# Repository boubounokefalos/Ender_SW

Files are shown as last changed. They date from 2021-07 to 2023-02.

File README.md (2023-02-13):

# Ender 3 Pro/V2 to Switchwire Conversion Release.2

This is a full conversion of the popular Ender 3 Pro/V2 to a Voron Switchwire. The motivation came from [Triano](https://github.com/walttriano) and [his awesome original conversion](https://github.com/walttriano/VoronUsers/tree/master/printer_mods/Triano/Ender_3Pro_Switchwire) that served as a starting point, however everything was re-designed from scratch (in order to follow the Voron guidelines and aesthetics more accurately). Another factor that led to this re-design, was the need to be able to enclose this printer in a, visually, pleasant and, structurally, functional way. The ingenious design of 5x MGN12H Linear Rails - 300mm (dual Y axis rail) from Triano was preserved and the printing volume is ~220x220x220.

# Release 2 Update Changelog:

- CAD files cleaned up.
- Small corrections to parts.
- Added printable deck files (still it's recommended to laser cut them though)
- Added different .dxfs for rear black panels (in case anyone wants to cut the panels from a material that is not same on both surfaces)
- Added the option to use the stock Ender 3 LCD screen.

# Rev.2 Update Changelog:

- Every change happened in order to improve the build process and the design overall.
- All screw sizes and types are properly documented in the CAD (soon there will be a conversion BOM also). Also no more “exotic” sizes, everything is according to what VORON is using officially.
- Current conversion’s enclosure is 100% compatible with the new update (except of the deck panels ofc).
- XZ Blocks improved fit for the X v-slots and are also modified to use 30mm BHCS (like the original SW).
- Y Axis, new front idler (in order to achieve a mounting point for the front grill), improved clearance for the rear Y motor mount. All use BHCS screws now.
- Split bed carriage with size and clearance corrections. Made uppon the design recommendation of Steve. Also Y belt clips have a bit more clearance on the upper side, in order to leave some space for spare belt 🙂
- XZ motors have thinner XZ tensioners to avoid the lower “split” (kudos to Steve for that ALSO).
- We are now using the original SW Spool Holder (for easier installation, due to clearance)
- Front Grills have now the LCD mount of the original SW. They also mount to the extended sides just by M3 screws.
- Rear Grills mount by M5x16 BHCS screws now. Also the inlet has moved to the side (in order to have a straight and easier connection with the PSU), this was also a recommendation by Steve and he was more than kind to share his original .F3D file. Both stock Ender and C14 inlets are compatible.
- Removed material from the grills, in order to save some plastic and cut down print time.
- PSU is now mounted parallel to the side extrusions and RS25 can be mounted in the front of the printer.
- Redesigned mounts for the Board and RPi (no more shelf and moooahr clearance!)

And last but not least…
-The side extensions. Front and rear side extensions are designed to extend the frame for aesthetical and a few practical reasons (clearance and NO MORE NOTCH). They are sturdy enough but keep in mind that you will not move around the printer by lifting it from there.

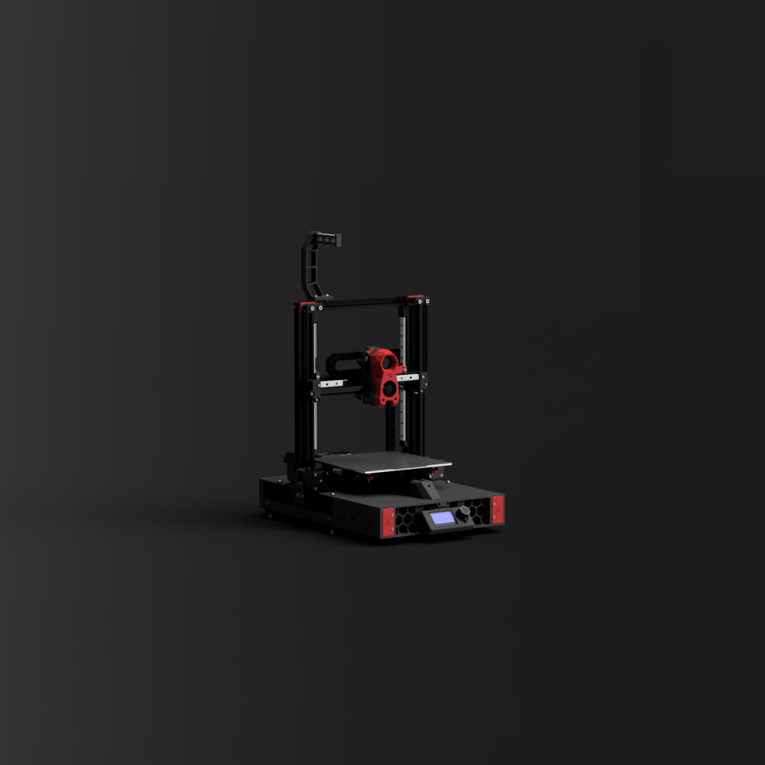
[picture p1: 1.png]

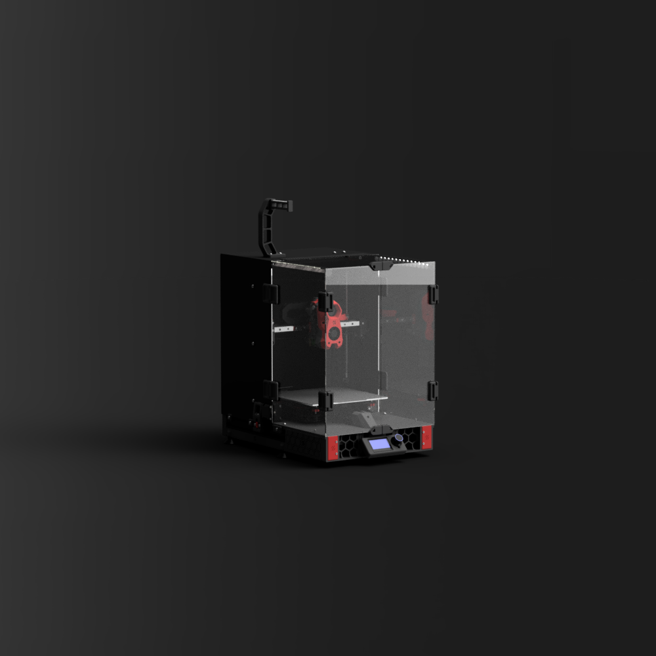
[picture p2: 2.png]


## Info

Various parts _can*_ be recycled from the Ender 3 Pro/V2, most important ones are:
- The frame (though a 310mm extrusion is needed for the X. You can chop the original one to length).
- The MeanWell PSU.
- The heatbed assemble.
- The original board.
- XYZ motors (as long as you can pull off the pulleys. An aftermarket 20mm motor is needed for the printhead extruder though).
- All the cables that don't go through the cable-chains (for there, silicone or PTFE cable is adviced).
- 4010 fan for the tool cooling.

*cheaping out in parts can lead into several problems, such as poor printing quality or, even worse, safety hazard. Keep that in mind and use parts from the official Switchwire BOM.

## Files

- Most of the printed part files needed for this conversion, are included in this git (you will only need to get the Stealthburner print files from the [official Switchwire git](https://github.com/VoronDesign/Voron-Stealthburner) ).
- CAD files (.f3d and .STEP) are provided, in order to help the building process, but they also serve as a BOM (in case you need to find proper screw lengths etc).
- DXF files in order to cut your enclosure panels.
- BOM (Sometime...)

## Credits

- Ofc to Triano, as his design served as base.
- To Steve (THE Steve!) for pointing out weak parts, that had to be redesigned, his tips and files and being a helpful person in general.
- To sdukan#9213 for his valuable help into troubleshooting the Ender 3 V2 differences, electronics (and in general).
- To all of this awesome community of people and especially the [ender_conversion_chat](https://discord.com/channels/460117602945990666/947303252372906014).
- To Voron design team for all the valuable resources and the solid base.

## Disclaimer

This is a very carefuly designed build.. however mistakes could have been made. By deciding to build this conversion, you are responsible for any possible damage done to the printer or even yourself.

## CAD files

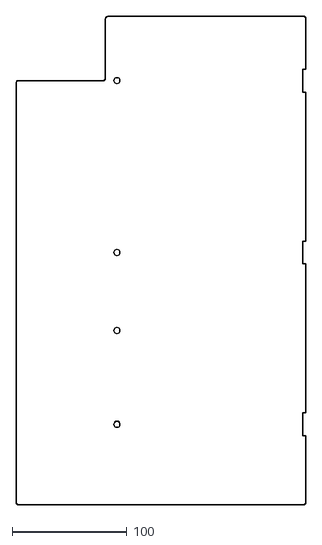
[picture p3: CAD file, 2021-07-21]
DXF/BLACK/M4_compatible/rear_side_panel_x2_M4_compatible.dxf
253.0 x 426.0

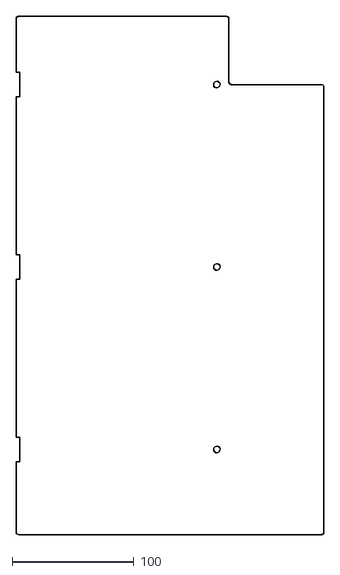
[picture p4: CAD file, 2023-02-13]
DXF/BLACK/rear_side_panel_right.dxf
253.0 x 426.0

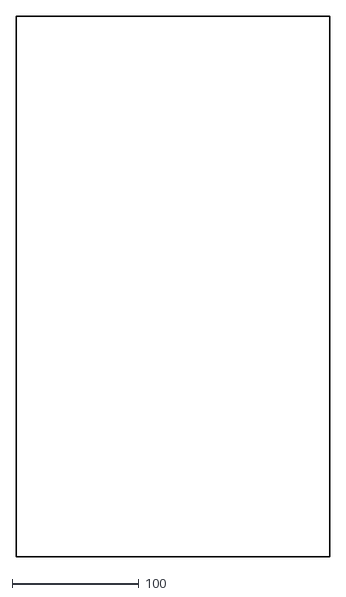
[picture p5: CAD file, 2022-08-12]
DXF/CLEAR/front_side_clear_x2.dxf
247.0 x 426.0

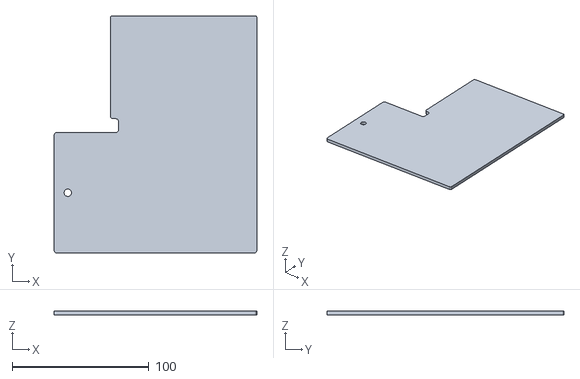
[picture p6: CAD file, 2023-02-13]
STLS/Decks_Printable/deck_left_mid.stl
148.0 x 173.0 x 3.00

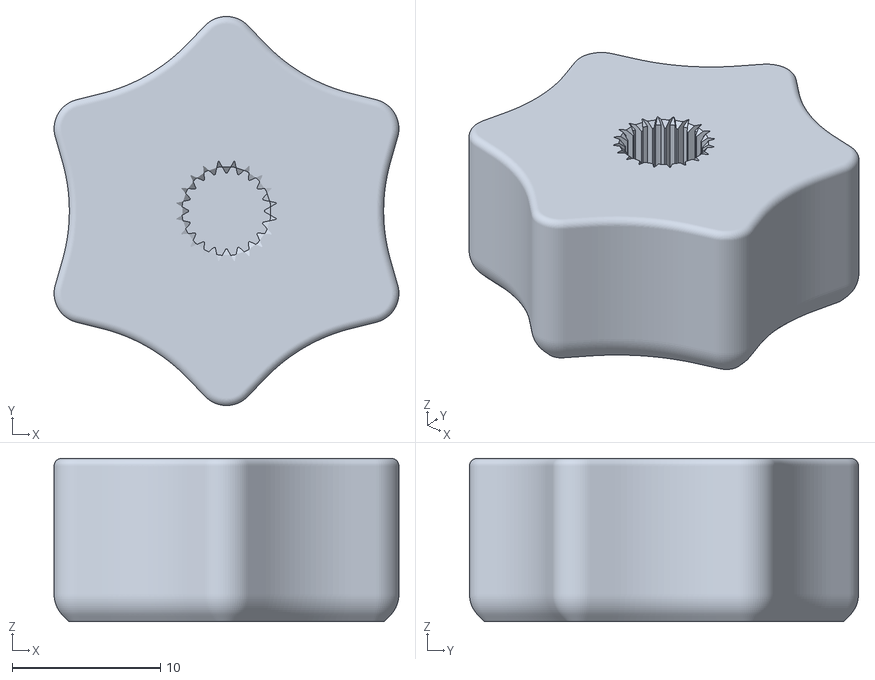
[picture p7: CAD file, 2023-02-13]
STLS/Electronics/Ender_Stock_Screen/[a]_knob.stl
23.3 x 26.2 x 11.0

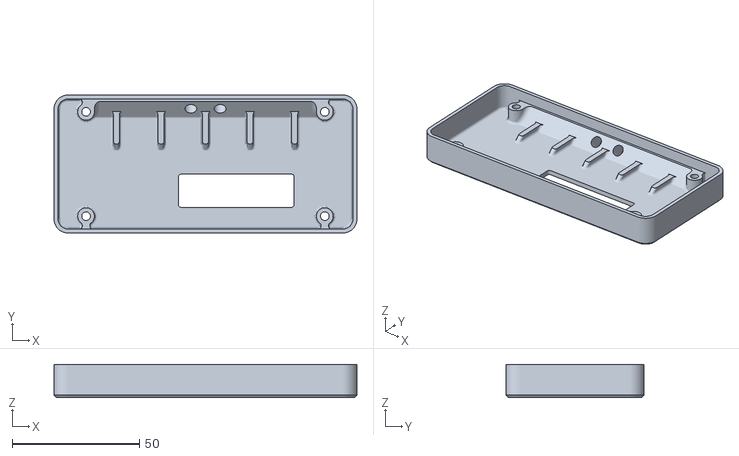
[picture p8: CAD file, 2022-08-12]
STLS/Electronics/Mini12864/lcd_case_rear_mini12864.stl
119.0 x 54.2 x 13.0

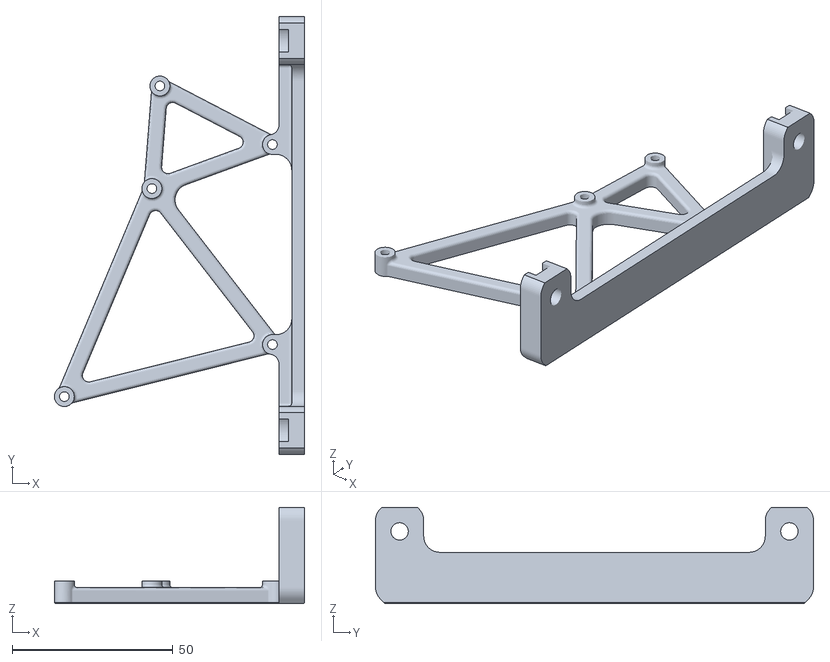
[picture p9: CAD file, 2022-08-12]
STLS/Electronics/skr_mini_e3_mount.stl
77.8 x 136.2 x 30.0

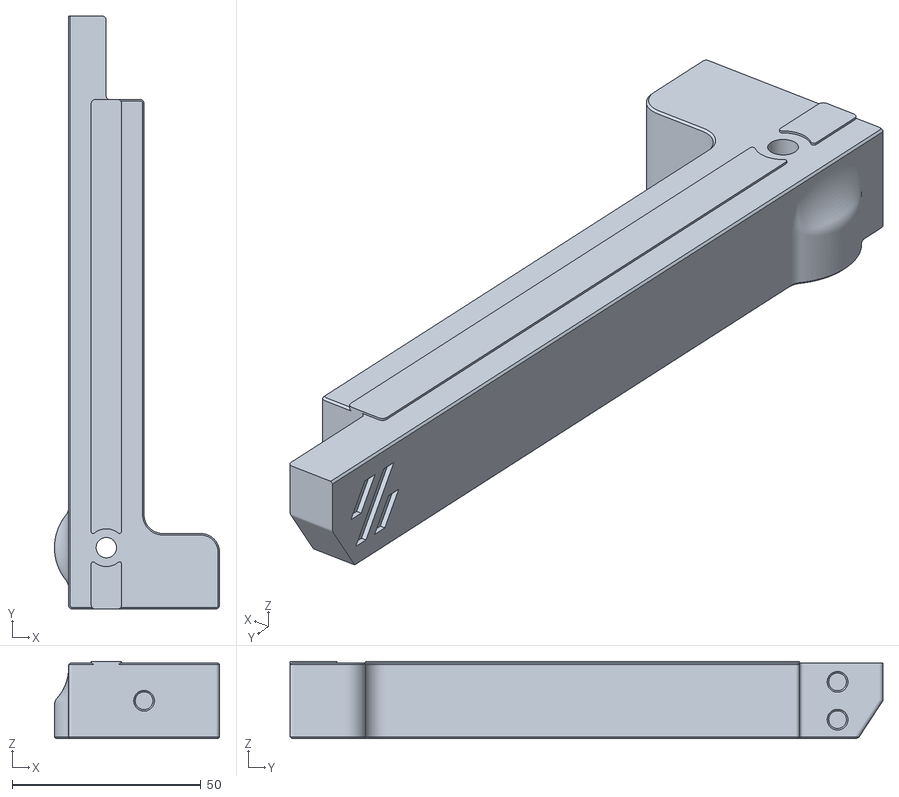
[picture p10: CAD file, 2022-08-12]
STLS/Extentions/rear_extention_right_b.stl
43.8 x 157.1 x 20.4

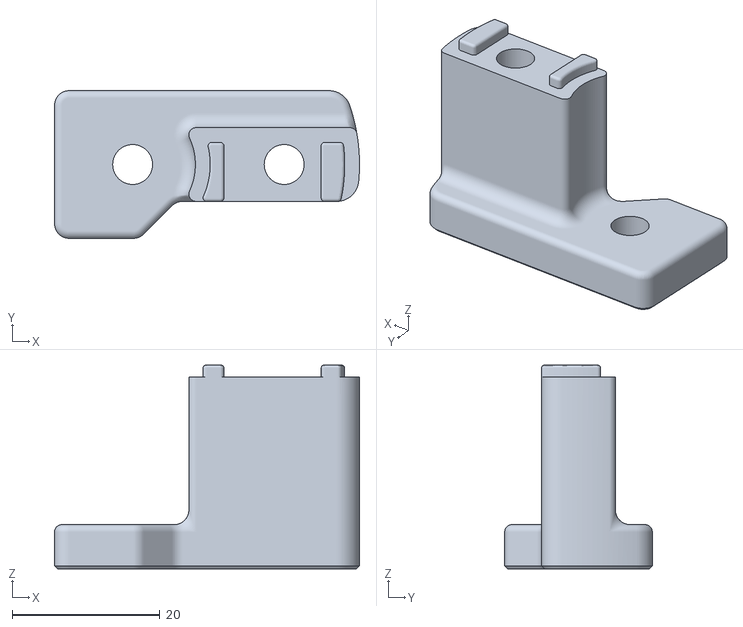
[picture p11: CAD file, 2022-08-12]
STLS/Gantry/XZ Axis/upper_idler_support_a_right.stl
41.3 x 20.0 x 27.6

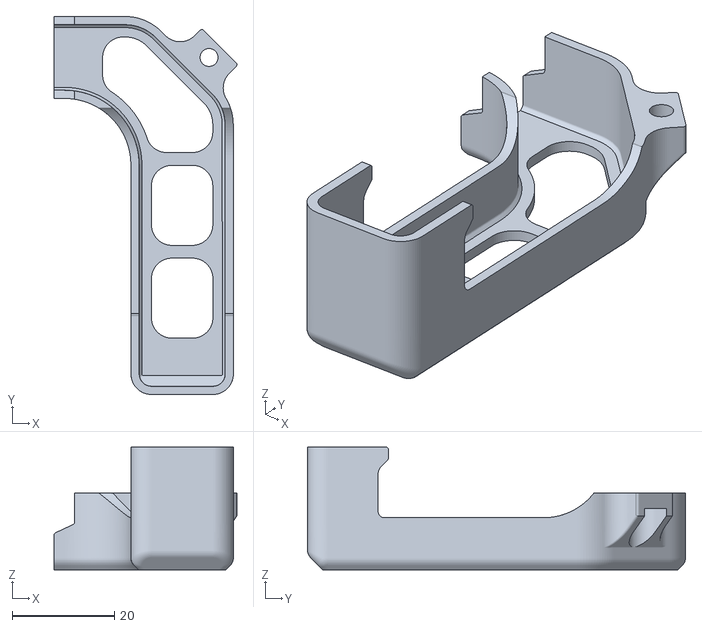
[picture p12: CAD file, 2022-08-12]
STLS/Gantry/XZ Axis/X Axis/[a]_xz_cable_cover.stl
35.7 x 73.8 x 24.0

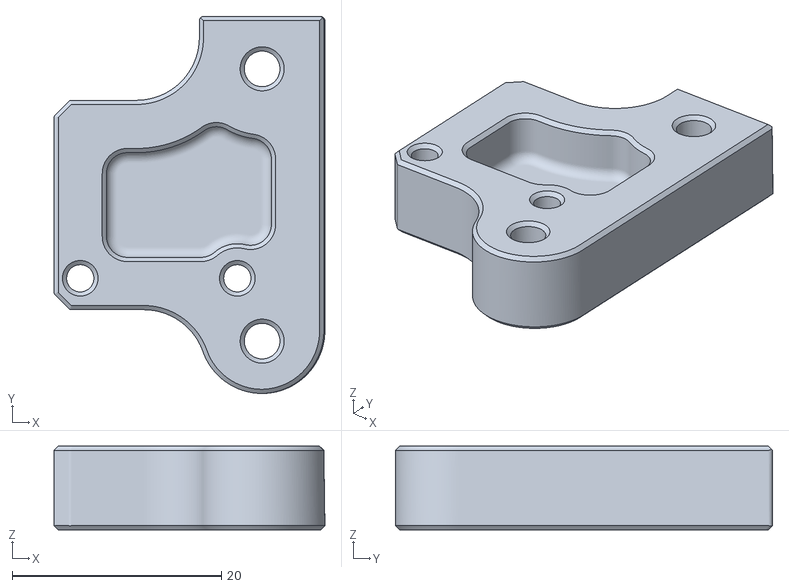
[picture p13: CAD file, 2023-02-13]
STLS/Gantry/Y Axis/[a]_y_axis_ls_mount.stl
25.9 x 36.0 x 8.00

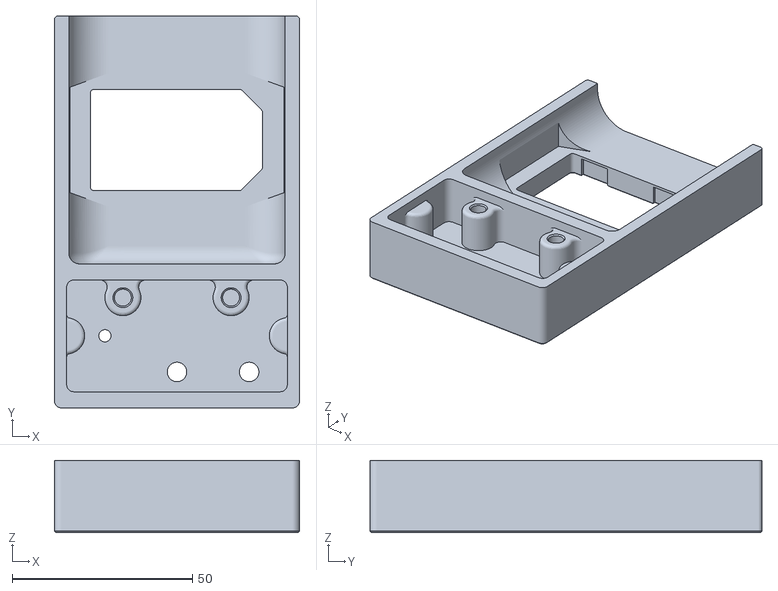
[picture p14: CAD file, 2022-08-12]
STLS/Grills/grill_rear_left_c14_inlet.stl
68.0 x 108.7 x 20.0

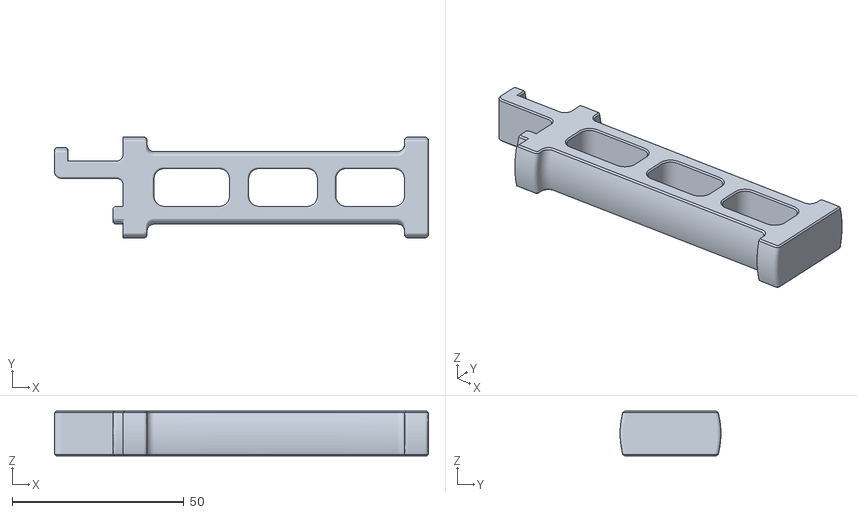
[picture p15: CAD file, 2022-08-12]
STLS/Misc/spool_holder.stl
109.0 x 29.4 x 13.0

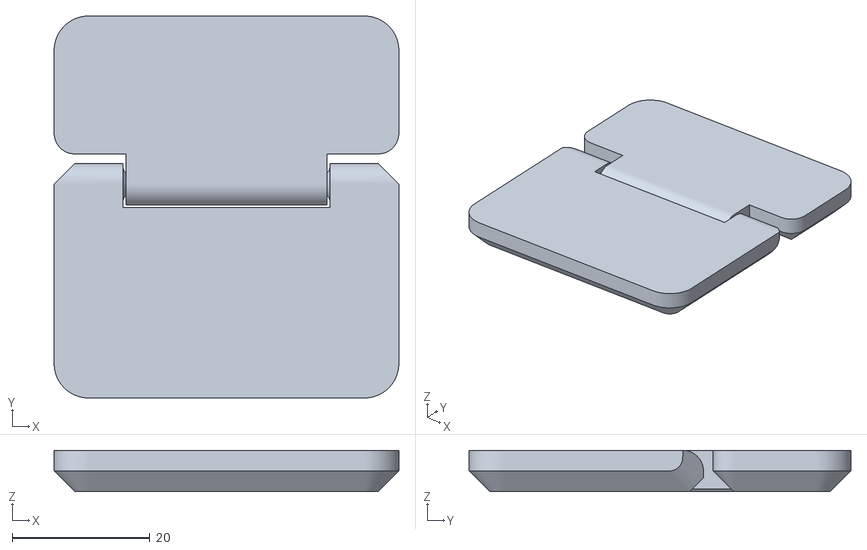
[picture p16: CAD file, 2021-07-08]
STLS/Panel_Mounting/Doors/door_hinge_x4.stl
50.0 x 55.4 x 6.00

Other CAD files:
STLS/Panel_Mounting/front_panel_bracket_left.stl
DXF/BLACK/deck_panel_right.dxf
DXF/CLEAR/front_top_clear.dxf
STLS/Decks_Printable/deck_left_rear.stl
DXF/BLACK/bottom_panel.dxf
DXF/BLACK/deck_panel_left.dxf
DXF/BLACK/rear_panel.dxf
DXF/BLACK/rear_side_panel_left.dxf
DXF/BLACK/top_rear_panel.dxf
DXF/CLEAR/front_clear_door_x2.dxf
STLS/Decks_Printable/deck_left_front.stl
STLS/Decks_Printable/deck_right_front.stl
STLS/Decks_Printable/deck_right_mid.stl
STLS/Decks_Printable/deck_right_rear.stl
STLS/Electronics/Ender_Stock_Screen/Grill.stl
STLS/Electronics/Ender_Stock_Screen/lcd_case_front_ender_lcd.stl
STLS/Electronics/Ender_Stock_Screen/lcd_case_rear_ender_lcd.stl
STLS/Electronics/Mini12864/lcd_case_front_mini12864.stl
STLS/Electronics/PS_4040_Slide_Mount.stl
STLS/Electronics/PS_4040_mount_x2.stl
STLS/Electronics/RPi_bracket.stl
STLS/Electronics/rs_25_mount.stl
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

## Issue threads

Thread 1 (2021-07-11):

Incorrect name for PS_2020_mount_b.stl

mdsamir15790, 2021-07-11:
Please update the PS_2020_mount_b.stl name. As per CAD it should be PS_4040_mount_b.stl

boubounokefalos, 2021-07-11:
@mdsamir15790 good observation! Thanks for that, the correct name is set now :)

Closed 2021-07-11.

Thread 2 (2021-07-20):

Add DXF for deck panels

retsamedoc, 2021-07-20:
It would be nice if you could create a DXF file for the deck panels (preferably in the same two piece configuration as the stock SW) so they could be laser cut?

boubounokefalos, 2021-07-20:
> It would be nice if you could create a DXF file for the deck panels (preferably in the same two piece configuration as the stock SW) so they could be laser cut?

Sure thing mate. Keep in mind though that these panels are cut from 3mm thick acrylic, while the front grills exceed the 4040 extrusions by 4mm (same as the printable deck panels). Will close this once they are added.

retsamedoc, 2021-07-20:
So 4mm material for deck panels would be ideal. I'm currently using coroplast (seems to be about 4mm thick).

boubounokefalos, 2021-07-21:
The DXF directory is updated with the files for the 2 decks, closing the issue now :D

Closed 2021-07-21.

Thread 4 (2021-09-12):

Question upper idler.

WalnutFox, 2021-09-12:
Just curious as to why the upper idler was changed, this would now require 2 m5x40 rather than 1. If this affects the BOM can you please update.

boubounokefalos, 2021-09-12:
The original upper idlers are protruding from the top extrusion. That prevents the printer from being able to be enclosed, without some ugly gimmick solution. Therefore, top idlers had to be re-designed from scratch.
Also keep in mind that the most accurate BOM for this conversion (at least for the screws), is the CAD itself.

Closed 2021-09-12.

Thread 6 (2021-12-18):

BOM

cchance27, 2021-12-18:
Love the look especially with the enclosure was looking into doing the conversion on my new Ender3Pro, but don't see any BOM for what can be reused vs what i'm going to have to order do you have one for the project? No XLSX or anything, just sorta got to look at the cad?

Especially for the enclosure parts

laserbeak, 2022-03-20:
Yes, is the enclosure the same as the Voron BoM?

Deep-Inspiration, 2022-03-20:
The enclosure is completely one-off and shares nothing with the official Switchwire.

laserbeak, 2022-03-21:
Gotcha. Works for me. Thanks.

Closed 2022-01-25.

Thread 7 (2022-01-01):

Missing M5x10 SHCS screw from Wiki

renjie-teo, 2022-01-01:
Hi! I've realised that M5x10 SHCS is a non-Voron BOM spec screw but its missing from the wiki, I had to order some midway building as i couldn't assemble my Y idler and motor, hope you can help add in the wiki for others!

Deep-Inspiration, 2022-01-25:
M5x10 SHCS isn't in the BOM but there are plenty of M5x10 BHCS in the BOM which should substitute just fine.

t0m-r1dd1e, 2022-03-18:
Also ran into this issue during assembly today. Fortunately I started with the Y axis so I can work on other things while I wait for these bolts.

bgct9a, 2022-04-16:
Another fastener issue is that BOM has only 6 M5x40 SHCS while the Cad Uses 8. You can recycle 2 of the m5 x 45's that are removed from the original Ender with some washers. This works as a solution for one of the Z bearing blocks.

bgct9a, 2022-04-16:
Going to Add 4 BHCS M5 x 35mm and 2 BHCS M3 x 14. The M3 x 14 was able to be substituted by an BHCS M3 x 16

boubounokefalos, 2022-08-13:
Closing this, since Rev.2 include all the proper sizes in the CAD model.

Closed 2022-08-13.

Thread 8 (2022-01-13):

Z Probe options and Klicky Probe

harshitgoel96, 2022-01-13:
Hi, I dont have access to genuine Omron Probe. I was look to use a clicky probe like quickdraw or Klicky probe. Do you have any working option for clicky probe? or can it be desinged around this conversion?

cchance27, 2022-01-19:
i haven't tested it but there is ... https://github.com/hymness1/VoronUsers/tree/master/printer_mods/hymness1/Quickdraw_probe_Voron_Switchwire

harshitgoel96, 2022-01-19:
That needs modification due to different extrusion size. And bed height.

I found this one to be very interesting option

https://github.com/salveoo/voronmods/tree/main/Switchwire%20Magprobe

boubounokefalos, 2022-08-13:
Closing, since there are lots of options by several members of the community.

Closed 2022-08-13.

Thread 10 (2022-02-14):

XZ Blocks don't quite fit v-slots, don't sit square, leg underneath extrusion doesn't extend all the way across.

strayr, 2022-02-14:
See image from interference analysis, the parts don't quite sit straight. There's a leg that needed extending as well that helps keep the parts square. I've made some fixes. https://github.com/strayr/Ender3_switchwire_fixes/tree/main/XZ-blocks.

I've done a T-slost version as well as I didn't want to cut up my ender 3.

I hope this is helpful, I'm not sure if I should be posting issue here or to triano's verion 2?

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

lowtolerance, 2022-03-18:
I’m in the middle of building this conversion, and I haven’t gotten around to assembling the XZ blocks. I’ll print these out and compare when I get a chance.

lowtolerance, 2022-03-25:
I forgot to actually print the modified XZ blocks made by strayr, and ended up using the cut edge of the Misumi extrusion like a double-sided plane to shave the parts until the alignment tabs fit snugly into the groove of the extrusion.

boubounokefalos, 2022-03-28:
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

Hello @strayr,

The reason behind this difference is to make the part "clamp" while it gets tightened by the screw on the v-slot groove of the extrusion. It was intended to be like that (this is also done to several other parts of the mod).

strayr, 2022-03-29:
I can't get it to sit straight on the extrusion, although that's probably
the corners not the v-slot, I went through a few iterations before I found
something that worked for me. Maybe you're printing in something that
shrinks less or is more compliant? I'm using eSun ABS+

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

boubounokefalos, 2022-08-13:
Hello mate,

This was carefully considered in the new Rev.2 and was modified accordingly.

Cheers!

Closed 2022-08-13.

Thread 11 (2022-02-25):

can this be made to support the mk52 bed

jaymoore962, 2022-02-25:
since the ender 3 has warping problems with the bed can you add support for the mk52 bed

Deep-Inspiration, 2022-02-25:
> since the ender 3 has warping problems with the bed can you add support for the mk52 bed

The Mk.52 is 17mm wider than the Ender bed and cannot physically fit in the Ender frame.  The only way to fit the Mk.52 is to buy an actual Switchwire frame.

boubounokefalos, 2022-03-08:
>

Correct! The dimensions are nowhere near, plus there is a whole different way the Y is designed.

Closed 2022-03-08.

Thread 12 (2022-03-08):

Ender 3 Compatibility

michaelmyc, 2022-03-08:
Is this compatible with the original Ender 3? I think the big issue will be the 40x40 extrusion on the Y, right?

boubounokefalos, 2022-03-08:
Unfortunately no. Apart from the Y extrusion, there are a few other key differences between 3 and 3pro.

Dilepa, 2022-03-20:
I started off with your mod on a ender 3, but can you please let me know what the other differences are other than Y?

Dilepa, 2022-03-20:
I have already modified the Y idler, Y motor mount and a 2020 spacer to lift the y axis. Anything else?

sparky3387, 2022-03-25:
Just want to leave a comment directing other people looking for this to [https://github.com/VoronDesign/VoronUsers/tree/master/printer_mods/Ultrawaffles/Ender_3_to_SW](https://github.com/VoronDesign/VoronUsers/tree/master/printer_mods/Ultrawaffles/Ender_3_to_SW)

Closed 2022-03-08.

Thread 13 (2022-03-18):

Can’t mount grills or 4040 extenders on Ender 3 v2

lowtolerance, 2022-03-18:
I just went to install the front grill on my Ender 3 v2 and realized that mine does not have tapped holes for the two outer 4040 extrusions, so I can’t mount the front and rear grills as designed.

I was thinking about modifying the front 4040 extenders so that the front grill bolts to them directly, and then the extenders could slot into the V-slot grooves, but I’m concerned that it won’t be strong enough with the weight of the enclosure and display.

Is it possible to buy new extrusions with the holes already drilled in the right places for mounting the Z profiles and the 4040 that goes between these two? Tapping the holes myself is not something I’m equipped for.

Any guidance on how I should proceed would be appreciated.

plasticboat, 2022-03-18:
I encountered the same thing. Honestly I just bought an HSS M5 tap and tap handle from Amazon and took my time. I was easily able to tap the eight holes required on the RH 4040 extrusion.

lowtolerance, 2022-03-18:
Hand tapping them didn’t even occur to me, but I guess it can’t be that hard if the holes are already there. I ordered a kit, thanks for the advise

plasticboat, 2022-03-18:
You're welcome. I do think the readme should warn people about this though in my opinion. I didn't realize it myself until I was pretty committed to this build.

t0m-r1dd1e, 2022-03-18:
Yeah grab a cheap tap set. They work fine for aluminum and you'll be glad you have them in the future.

lowtolerance, 2022-03-19:
I got a cheap tap set for $10 and managed to tap all 16 of these holes in about 30 minutes. Thanks for the advice.

Closed 2022-03-19.

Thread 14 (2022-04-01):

update printer.cfg

tol2cj, 2022-04-01:
Please correct usage of default parameter values in cancel_print and pause
 like this:
#default_parameter_X: 220
#default_parameter_Y: 220
#default_parameter_Z: 10
gcode:
    {% set X = params.X|default(220) %}
    {% set Y = params.X|default(220) %}
    {% set Z = params.X|default(10) %}

boubounokefalos, 2023-02-13:
Due to a wide variety of configurations nowdays,
I will no longer be including configuration files.

Cheers!

Closed 2023-02-13.

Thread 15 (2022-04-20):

Missing foot screws from CAD and BOM

ndanyluk, 2022-04-20:
Hi, thanks so much for your awesome work on this!

I'm opening this issue because when searching through the .f3d file I can't seem to find any screws attaching the feet to the frame.  I assume since the extensions are 20mm tall that we probably want something like M5x25 or 30mm but I couldn't tell.  Do you have a particular screw spec'd for this part?

About to order my screws for the build and want to be sure I grab em all :)

boubounokefalos, 2022-08-13:
Hello mate,

No screw size is stated regarding the feet due to the fact that most people use different feet (regardless the included air compressor rubber ones).

Closed 2022-08-13.

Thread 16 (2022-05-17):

cover_4040_extrusion_cut_enderV2 is not wide enough ..

piotrb, 2022-05-17:
On my V2 the cutout is ~40mm (not 35 as this STL expects) ..
it also looks like its been cut out "more"? .. the intended clip in the current design won't catch on anything there ..

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

boubounokefalos, 2022-05-17:
> On my V2 the cutout is ~40mm (not 35 as this STL expects) .. it also looks like its been cut out "more"? .. the intended clip in the current design won't catch on anything there ..
>
> 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

Unfortunately there are quite a few iterations of Ender V2 with differences I cannot follow up (since I don't own this machine). This specific cable cover was designed with the help of a friend that had this exact dimensions (on his Ender 3 v2)

Closed 2022-05-17.

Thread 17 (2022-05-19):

4040_rail_tool stl missing

bob92553, 2022-05-19:
[4040 rail tool.zip](https://github.com/boubounokefalos/Ender_SW/files/8734505/4040.rail.tool.zip)

matthewdolman, 2022-12-04:
Thank you!

Closed 2023-02-13.

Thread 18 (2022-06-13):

mounting the enclosure

flow1990, 2022-06-13:
I can't find anything about mounting the printed parts to the enclosure. Is the tape used here?

boubounokefalos, 2022-06-25:
It's the exact same way as the original SW (VHB tape)

Closed 2022-06-25.

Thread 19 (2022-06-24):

Ender 3 V2 - X extrusion is wrong size ..

piotrb, 2022-06-24:
Seems like the model calls for a 310mm X gantry extrusion .. seems like my Ender 3 v2 uses a 350mm one there.

I'm reluctant to cut it (since once its done there is no going back there ;) .. really gotta get all my parts assembled and ready before I do this next step .. was hoping I was going to be able to be a bit gradual, but this one part seems to require a permanent modification.
It seems like the whole design depends on that extrusion being a but shorter than its wide so it seems like its kind of key to note that for folks.

The instructions should include something about potentially needing to do this :)

Perhaps in the wiki around the frame section.

boubounokefalos, 2022-06-25:
This is stated at the first lines of the "Info" section (310mm info for the X). This is not a modification that can be done gradually.

Closed 2022-06-25.

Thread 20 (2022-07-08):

BOM Difference: MGN12 Rails

ardichoke, 2022-07-08:
The BOM page in the wiki should note that a 5th MGN12 rail is needed for this conversion, since the official BOM for the Switchwire only requires 4.

I'd submit a pull request for it.... but you know, can't do PRs on the wiki repo. Thanks GitHub.

boubounokefalos, 2022-08-13:
Hello mate,

5xMGN12 is stated on the README :)

ardichoke, 2022-08-14:
Sure, but if you're going to have a BOM in the Wiki that lists the additional items you need, it should be complete, and it currently isn't. I ordered parts based on the stock BOM + the items listed in the BOM in the wiki and then had to order another rail once I started actually building because of that.

Closed 2022-08-13.

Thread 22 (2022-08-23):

BOM?

lordmach, 2022-08-23:
Where is the BOM? I cannot find it anywhere in the files. Thank you.

boubounokefalos, 2022-08-23:
BOM will be available soon (only for Rev.2) as stated.

lordmach, 2022-08-23:
I watched this build on Steve's channel and got an Ender to start it. Do you mind sending my the BOM? Thanks for all your effortsBTW.

boubounokefalos, 2022-08-23:
The BOM will be released once it's fully ready for everyone. Till then, CAD serves as BOM.

Cheers :)

lordmach, 2022-08-23:
OK. Ill get it from Steve.

Thanks anyway...

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

--
Regards,

Joe Costa

aforww, 2023-01-21:
It's been five months, any updates?

boubounokefalos, 2023-01-21:
> It's been five months, any updates?

Robotrogue has uploaded a basic BOM that can help you >>> https://github.com/RobotRogue/Enderwire_Docs

Closed 2022-08-23.

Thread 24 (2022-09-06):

Rev. 2

DoCJEaa, 2022-09-06:
Hello,
Is there a way to reach you via Discord or something like that? I have a few ideas for Rev. 2.

petternilsen, 2022-09-06:
Yes, the voron discord have a thread under switchwire for ender conversions.

LukasM82, 2022-09-08:
Go here, it's called #ender_conversion_chat as a sub thread under the voron_switchwire_questions

https://discord.com/channels/460117602945990666/947303252372906014

Closed 2022-09-09.

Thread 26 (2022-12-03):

Is there a BOM for this conversion ?

Neiizo, 2022-12-03:
I would really like to make the conversion, but without a conversion, it feels kind of weird.
At first, i thought i would buy the entire sw bom, without the extrusions, psu, mainboard, hotend and rpi, but I'm assuming some of the screws can be conserved, and some stuff need to be adapted to the extrusion size of the ender 3 pro. So is there a complete BOM for this ?

FGRCL, 2022-12-04:
I think the BOM is still a work in progress. #22

boubounokefalos, 2023-02-13:
RobotRogue was kind enough to work in [one](https://github.com/RobotRogue/Enderwire_Docs/blob/main/README.md)

Cheers!

Closed 2023-02-13.

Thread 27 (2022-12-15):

Ender 3 Max and CR10 Y carriage adapter

Krisstank, 2022-12-15:
I modified and created a remix for the Y carriage to allow for the Ender 3 Max and CR10 plates wasn't sure where to contact or upload it.

I'll be doing a bunch more mods to adapt it and will keep the files contained as the build goes forward for you future uploads.

https://www.printables.com/model/340607-voron-switchwire-ender-3-max-and-cr10-y-adapter-fo

boubounokefalos, 2023-02-13:
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

Glad these worked out for you as a base!

Printables and Github are convinient for people.

Cheers!

Closed 2023-02-13.

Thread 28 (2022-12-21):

CAD shows wrong screw length for the display case and for fastening the case to the front middle grill

erazor666, 2022-12-21:
It shows as 4x m3x12mm for assembling the case, too short and I had to go for 16s, same with the display case to the grill 2x m3x12, has to be 16s.

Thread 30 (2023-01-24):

Quantity error

asmalloo2, 2023-01-24:
This part says 1 when 8 are needed.  Can we change that

https://github.com/boubounokefalos/Ender_SW/blob/Rev.2/STLS/Misc/2mm_spacer.stl

boubounokefalos, 2023-02-13:
> This part says 1 when 8 are needed. Can we change that
>
> https://github.com/boubounokefalos/Ender_SW/blob/Rev.2/STLS/Misc/2mm_spacer.stl

Hey mate,

Spacer's name does not mention quantity, these serve as helpers and are inlcuded just in case one has longer screws than the actual needed.

Cheers!

Closed 2023-02-13.

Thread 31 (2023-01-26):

Y motor mount wrong fastener length

JagJagula, 2023-01-26:
The cad and stl call for m3x30,Printed today and m3x30 is too short
M3x30 wont make it to the stepper motor threads

boubounokefalos, 2023-02-13:
> The cad and stl call for m3x30,Printed today and m3x30 is too short M3x30 wont make it to the stepper motor threads

Y_Motor_Mount needs **m3x40,** exactly as it appears in the CAD.

Closed 2023-02-13.

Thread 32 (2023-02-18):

[a]_y_axis_ls_mount.stl

bwork1, 2023-02-18:
Might need to reverse the center space or flip the recessed holes

Closed 2023-02-22.

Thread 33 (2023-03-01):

Voxlab Aquila

smccloud, 2023-03-01:
Will this conversion work on a Voxlab Aquila?  Its very similar to an Ender 3 V2, just a different mainboard (which I am planning on swapping out anyway) and the stock screen is sideways instead of vertical like on the Ender 3 V2.

boubounokefalos, 2023-03-02:
> Will this conversion work on a Voxlab Aquila? Its very similar to an Ender 3 V2, just a different mainboard (which I am planning on swapping out anyway) and the stock screen is sideways instead of vertical like on the Ender 3 V2.

Probably yes, except of the y bed carriage.

However, the3dhammer #1915 (from discord), made a custom y bed carriage that fits Voxlab Aquila.

You can find it [here](https://www.printables.com/model/411425-voxelab-aquila-switchwire-y-axis-bed-carriage/files)

Closed 2023-03-02.

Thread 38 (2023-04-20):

skr bracket leaves no room for usb

traceoption, 2023-04-20:
the skr bracket, mounted as the cad drawing depicts, leaves the USB port too close to the right main 4040 bracket.  I do like where its mounted, and looking for a 90 degree usb cable.

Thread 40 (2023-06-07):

Request support bracket for bigtreetechs board.

xXHexaKillXx, 2023-06-07:
Hi i love your work and actaually working my way through the conversion as we speak. I notice that the board you support skr mini e3. But i have skr 3 board. Was wondrring if you can help me out?

grungywamp, 2023-07-24:
[SKR 1.4 4040 Mount.zip](https://github.com/boubounokefalos/Ender_SW/files/12141347/SKR.1.4.4040.Mount.zip)
mount I am using for 1.4 board - file is parametric and should be easy to modify

xXHexaKillXx, 2023-07-24:
Thanks. Do you perhaps convert your stuff to support autocad format

grungywamp, 2023-08-06:
sorry mate, F360

xXHexaKillXx, 2023-08-06:
Oh regarding the feet adjustment are those just thread intonthe frame of the ender?

grungywamp, 2023-08-06:
SKR_Hole_D - hole diameter for M2 self tapping screws
SKR_Pad_H - height of pad above frame to give clearance for soldered connections

FRMM - **FR**a**M**e **M**ount parameters - set up for M5x0.8x10 BHCS and M5 hammer nut to secure to 4040 extrusion

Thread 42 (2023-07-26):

DXF bottom panel appear out of date

Ixian, 2023-07-26:
Viewing the dxf panel bottom_panel.dxf it appears out of date with the current CAD drawing. It only shows 1 screw hole when the design calls for more. I haven't checked the exact dimensions for the other panels but are they up to date with the current design? I want to send them off to Sendcutsend but ran in to this issue.

Thanks! Appreciate all the work on this.

Millerboy3, 2023-08-21:
what did you end up doing? I was just about to have mine cut as well didn't notice this until you said something.

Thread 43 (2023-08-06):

part y_motor_mount_bracket_enderV2

grungywamp, 2023-08-06:
Part appears to be artifact? -
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

In cad, part is inside the rear end of the y-axis 4040 by 10mm.

If part is needed for full range of motion for bed, then hardware should be updated from M5x0.8x16 BHCS to M5x0.8x25 BHCS. However, this will offset the rear grills 10mm and prevent the rear middle grill from mounting as is.

boubounokefalos, 2023-08-06:
This part is to extend the y motor mount in order to reach the edge of the grill **specifically for the Ender V2 derivative.** (due to the fact that it has a shorter y extrusion)

grungywamp, 2023-08-06:
And here I was thinking it was just a different mainboard, screen a few cosmetics.  Thanks for the info

Closed 2023-08-06.

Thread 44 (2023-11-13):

cover_4040_extrusion_cut_enderV2.stl

Bersaker, 2023-11-13:
Hi. I have a Ender 3v2. The cutout in the frame is 40x40mm.This file is 35x40. Can you add 40x40 ?

ccfman2004, 2024-02-23:
I have the same issue the model in the v2 STL is too short.

A-Rushton, 2024-04-11:
I had this issue too, i just scaled the part in SuperSlicer in the single axis and it did the job as a work around

absak0, 2024-04-11:
As an alternative I used this STL and it worked great  :

https://www.printables.com/model/224831-2040-mgn12-alignment-tool

A-Rushton, 2024-04-11:
I think this comment was intended for Issue #50 @absak0 ?

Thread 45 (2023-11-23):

Whole dfx plate for lasercutting

jackmiller1986, 2023-11-23:
Hi can you add the whole plates from the buttom , for lasercutting ind dfx files pls.

jackmiller1986, 2023-11-23:
because i want it in whole not in single printed parts

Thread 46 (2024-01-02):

Not everything matches to my Ender 3 Pro

GrzesiuS, 2024-01-02:
Is something wrong with my Ender 3 Pro or I missed something? I printed all elements but it doesn't fit to my Y axis. It looks like my Ender 3 has a different construction and the frame profile is slightly moved to the end. It causes some issues because I can't mount the step motor and the rest of the elements.

https://photos.app.goo.gl/wZVkKsc1fxiVbf6e9
https://photos.app.goo.gl/VmHkx89yoPZ2q3Ks9

midikeyboard, 2024-01-02:
there is a printable Y spacer you need to install at the back of the extrusion

GrzesiuS, 2024-01-02:
I can't see anything in files:
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

The only spacer I see is:
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

But it's for the motor mount and it moves the motor to the back even more but I can't install the motor mount because it looks like my Y axis frame profile is already moved slightly to the end of the printer

GrzesiuS, 2024-01-02:
I draw some lines to show more clearly what's wrong.

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

The frame for Y axis is mounted slighlty closer to the end of the printer so I can't match wholes from the grill and motor mount

midikeyboard, 2024-01-02:
i can recommend you to watch this video on how to assemble your motor mounts before actually mounting them.
as i think you're supposed to mount the stepper to the motor mount before mounting it assembled as a whole through the holes in the printed spacer you mentioned previously.

https://www.youtube.com/watch?v=zTK_sYR6u8Y

GrzesiuS, 2024-01-02:
"P.S: have you relocated your Y extrusion slighty to the front?"

Nope, the frame doesn't have other holes to move it to the front. I already checked it. I see two possibilities here.
1. I need to make new holes in the frame and move it to the front
2. Print brackets and use them to move the frame

The second option sounds easier because I can adjust the position using brackets but I'm a little bit worried but the stability of such construction.

midikeyboard, 2024-01-02:
when i did my conversion i went from the default 4 holes to only the 2 front holes. and tapped the 2 missing ones by hand. does your extrusion have 4 holes as well?

GrzesiuS, 2024-01-02:
> when i did my conversion i went from the default 4 holes to only the 2 front holes. and tapped the 2 missing ones by hand. does your extrusion have 4 holes as well?

I did the same, thank you!

Closed 2024-01-02.

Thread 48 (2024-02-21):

Voron Switchwire cr10

StalkFPV, 2024-02-21:
Hi everyone, it's a shame that this doesn't exist for CR10.

because I have a cr10 v1 lying around it would have been nice to transform it into voron switchwire

midikeyboard, 2024-02-22:
https://www.printables.com/model/340607-voron-switchwire-ender-3-max-and-cr10-conversation

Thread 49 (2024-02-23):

Errors in the Wiki docs

ccfman2004, 2024-02-23:
Some of the links in the Wiki Docs are incorrect.  They have STLS in the path when it should be STL as an STLS folder doesn't exists in this repository,

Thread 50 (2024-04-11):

MGN Rail Alignment Tool

A-Rushton, 2024-04-11:
During the build process of my Voron 2.4 i found the rail alignment tool invaluable to get proper alignment on the aluminium extrusions. Would be nice to have that tool for this project too (one that fits on the 4040 extrusion for the y axis to enable correct alignment)

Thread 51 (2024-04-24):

BOM not found

msg94, 2024-04-24:
Can you tell me where the BOM is or the link?

midikeyboard, 2024-04-25:
> Can you tell me where the BOM is or the link?

there is no BOM as mentioned in the readme. you can use the CAD file for sourcing and guiding

ThunderClap86, 2024-06-01:
All screw sizes and types are properly documented in the CAD (soon there will be a conversion BOM also). Also no more “exotic” sizes, everything is according to what VORON is using officially.

Any word when the BOM might be released, cannot use CAD currently as my hardware prevents it.

midikeyboard, 2024-06-02:
i dont have an update but you could look into this repo:

https://github.com/RobotRogue/Enderwire_Docs

YoungHillionaire, 2024-08-05:
Use the siboor ender switchwire fasteners kit
It has all the necessary screws
I just converted my Ender 3 Neo
It was missing an M3X30 SCHS only
Had 15 screws while CAD uses 16
4 for X motor mount and 4 for Z motor mount
And 4 for each z bearing block
Luckily it was included in the spares

christianbundy, 2024-09-30:
Trust at your own risk: I went through the "gantry" component and compiled a BOM, here's what I found:

- X Axis Assembly
  - 2020 Extrusion 310mm
  - MGN12 Linear Guide Subassembly, 12H
    - MGN12 Linear Guide Rail 300mm
    - 4 × M3x8 SHCS
  - Z Bearing Block — Left
    - 2 × M3 Threaded Insert
    - 2 × M5x40 SHCS
    - 4 × M3x30 SHCS
    - 2 × M3x12 SHCS
  - Z Bearing Block — Right
    - 4 × M3 Threaded Insert
    - 4 × M3x30 SHCS
    - 2 × M5x40 SHCS
  - XZ Block — Right
    - 4 × F695-2RS Bearings
    - 4 × M5 1mm Spacer
    - M3x16 SHCS
    - 2 × M5x30 BHCS
    - M5x10 BHCS
  - XZ Block — Left
    - 4 × F695-2RS Bearings
    - 4 × M5 1mm Spacer
    - M3x16 SHCS
    - 2 × M5x30 BHCS
    - M5x10 BHCS
  - Stealthburner Assembly: NOT INCLUDED (Assumed to be stock, no changes required)
- Z Motor Assembly
  - NEMA17 Motor
  - GT2 20T 6mm Pulley
  - M3 Threaded Insert
  - 2 × M5x16 BHCS
  - 4 × M3x30 SHCS
  - M3x40 SHCS
- X Motor Assembly
  - NEMA17 Motor
  - GT2 20T 6mm Pulley
  - M3 Threaded Insert
  - 2 × M5x16 BHCS
  - 4 × M3x30 SHCS
  - M3x40 SHCS
- Upper Block — Left
  - 4 × F695-2RS Bearings
  - 4 × M5 1mm Spacer
  - 2 × M5x40 SHCS
- Upper Block — Right
  - 4 × F695-2RS Bearings
  - 4 × M5 1mm Spacer
  - 2 × M5x40 SHCS
- Z Belt
- X Belt

Totals:

| Part                          |   Quantity |
|:------------------------------|-----------:|
| 2020 Extrusion 310mm          |          1 |
| F695-2RS                      |         16 |
| GT2 20T 6mm Powge             |          2 |
| M3 Threaded Insert            |          8 |
| M3X30 SHCS                    |         16 |
| M3x12 SHCS                    |          2 |
| M3x16 SHCS                    |          2 |
| M3x40 SHCS                    |          2 |
| M3x8 SHCS                     |          4 |
| M5 1mm Spacer                 |         16 |
| M5X10 BHCS                    |          2 |
| M5x16 BHCS                    |          4 |
| M5x30 BHCS                    |          4 |
| M5x40 SHCS                    |          8 |
| MGN12 LINEAR GUIDE RAIL 300mm |          1 |
| NEMA17                        |          2 |
| X Belt                        |          1 |
| Z Belt                        |          1 |

I'm a bit skeptical, because elsewhere I've read "20 × F695-2RS" pretty consistently, so I'd advise double-checking the CAD and/or just ordering a few extras in case I've made some mistakes.

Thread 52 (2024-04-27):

CAD files for stock Ender screen

YoungHillionaire, 2024-04-27:
missing CAD files for stock Ender 3 screen

nikitos4319, 2024-04-27:
it's there, just hidden
Front Grill v1 -> grill_front_middle_Ender_screen_assembly

YoungHillionaire, 2024-04-29:
Thanks missed it

Closed 2024-04-29.

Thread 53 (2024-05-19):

Any plan could use CR6 SE upgrade to Voron Switchwire like?

mysy200, 2024-05-19:
Any plan could use CR6 SE upgrade to Voron Switchwire like?
I have one CR6 SE not use for long time... too slow compare to my voron 0.2

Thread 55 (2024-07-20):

X carriage missing from repo

YoungHillionaire, 2024-07-20:
I am almost finished assembling my Enderwire
doing my gantry now
When I realized that x carriage is missing from the repo

thetic, 2024-07-20:
use the stock switchwire carriage/toolhead stuff

YoungHillionaire, 2024-07-27:
> use the stock switchwire carriage/toolhead stuff

Thanks.
Might use XOL toolhead instead

Closed 2024-07-27.

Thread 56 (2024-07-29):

Missing X_Carriage files

volt64bolt, 2024-07-29:

thetic, 2024-07-29:
https://github.com/boubounokefalos/Ender_SW/issues/55

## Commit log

2021-07-08 add decks
    [front_left.stl, front_right.stl, rear_left.stl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]
2021-07-08 fix orientation
    [PS_2020_mount_b.stl]
2021-07-08 added Mini12864 mount
    [mount_mini12864.stl]
2021-07-09 Added config file
    [E3_mini_V2_Ender_SW.cfg]
2021-07-11 fix name typo per request
    [PS_4040_mount_b.stl]
2021-07-21 Updated the design on some parts, added DXF for decks and M4 compatible rear panels
    [cover_4040_extrusion_cut_enderV2.stl, deck_left.dxf, deck_right.dxf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]
2022-08-12 Original Commit
    [cover_4040_extrusion_cut.stl, cover_4040_extrusion_cut_enderV2.stl]
2022-08-15 Fix clearance on y_idler_b part
    [y_idler_b.stl]
2022-08-17 Added cable routing cut for right deck
    [deck_panel_left.dxf, deck_panel_right.dxf, deck_panels_x2.dxf]
